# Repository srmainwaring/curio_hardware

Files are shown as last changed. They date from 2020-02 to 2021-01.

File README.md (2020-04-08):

# Curio Hardware

Addition parts for a Sawppy rover.

## Overview

This repository contains [FreeCAD](https://www.freecadweb.org/) and
STL files for additional accessories for
[Roger Chen's Sawppy rover](https://github.com/Roger-random/Sawppy_Rover).

The parts have been printed on a Prusa i3 mk3S printer using PTEG
filament. G-code was generated using PrusaSlicer configured with the
print settings described in the
[Sawppy Rover documentation](https://github.com/Roger-random/Sawppy_Rover/blob/master/docs/Print%20Overview.md).

## Bogie stops

The stops are to prevent the bogie arm attached to the middle wheel
rising from rising above the rear rocker arm and damaging the
servo wires.

***Printing:***

- Approx. 40 mins for a pair

***Assembly:***

Fit the stops with a M3 threaded heat insert and afix to the inside
slot of each front bogie arm with a M3 square nut and M3 x 16mm socket
head screw.

## RPLidar A1 mounting plate and cowling

The mounting plate and cowling are for fixing a Slamtec RPLidar A1
onto a Sawppy rover.

***Printing:***

- Mounting plate: approx. 2h 30min
- Cowling: approx. 5h

The cowling requires support and will need to be cleaned up post-print.
It may help to clean the holes in both the mounting plate and cowling
with a 3mm drill.

***Assembly:***

The mounting plate attaches to the front left corner of the main
body box. You will need to remove the body corner to insert
8 M3 square nuts into the T-slot into which
8 M3 x 16mm socket head screws will be fixed.

Prior to attaching the mounting plate to the rover, fix the
RPLidar A1 USB-to-TTL board to the underside of the
mounting plate. Make sure it is aligned so the ribbon cable comes up
and through the rectangular slot. Attach the ribbon cable to the
laser scan assembly then fix to the top of the plate. You may also
wish to insert the micro-USB cable into the USB-to-TTL board before
attaching as it is awkward (but not impossible)
to attach once assembled.

Place the cowling over the laser scanner and check the motor is clear
and the scan drum can rotate without obstruction. Then fix the
cowling and mounting plate to the rover body box with the
M3 x 16mm screws.

## Battery holder

This is an additional battery holder for securing a 5V 2A power bank
for the Raspberry Pi. It has been dimensioned to hold a
RAVPower RP-PB052 22000mAh power bank, but can be easily modified
for other models.

***Printing:***

- Approx. 4h for a pair of supports.

***Assembly:***

The battery holder comprises a pair of supports and is mounted on the
side rails of the main body box to the rear of the differential brace.
You will need to remove a rear body corner to insert 8 M3 square nuts
into the T-slot into which 8 M3 x 12mm socket head screws will be fixed.
Insert 4 M3 square nuts into the underside slot of the upper rail and
4 M3 square nuts into the topside slot of the lower rail.

The first support can be set up flush against the differential brace.
There should be a gap of approx. 40 mm between the two supports.  

## License

This software is licensed under the BSD-3-Clause license found in
the LICENSE file in the root directory of this source tree.

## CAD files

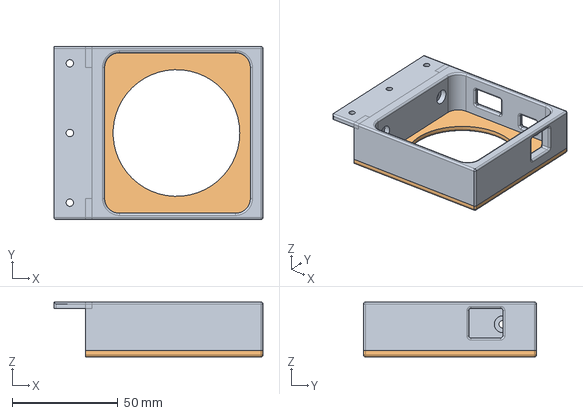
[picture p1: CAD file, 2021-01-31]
freecad/TPLinkAC750_Tray.FCStd
99.0 x 82.0 x 26.0 mm
TPLinkAC750_Tray_Body
TPLinkAC750_TrayBase_Body

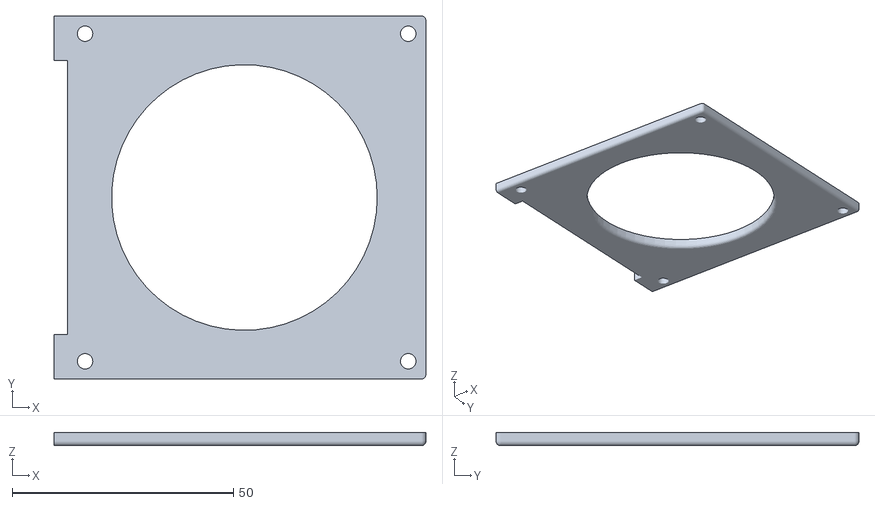
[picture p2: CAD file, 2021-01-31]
stl/TPLinkAC750_Tray_Base.stl
84.0 x 82.0 x 3.00

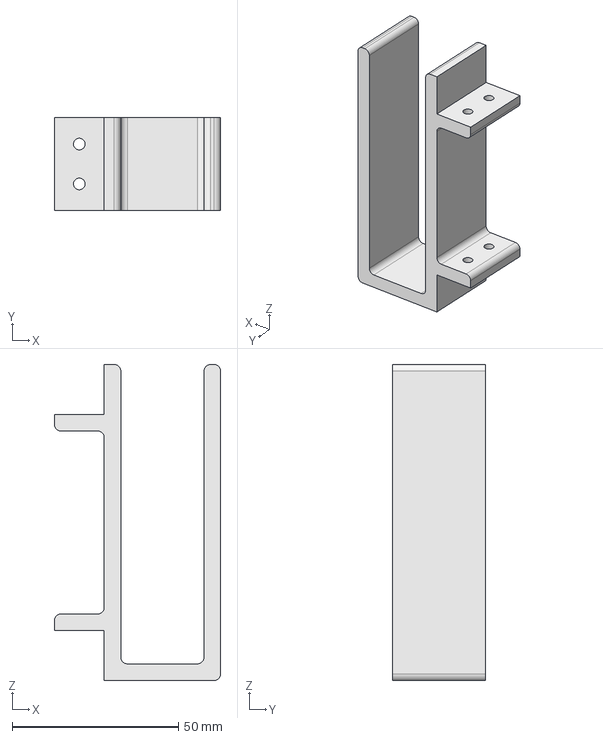
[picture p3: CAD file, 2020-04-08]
freecad/Battery_Holder.FCStd
50.0 x 28.0 x 95.0 mm

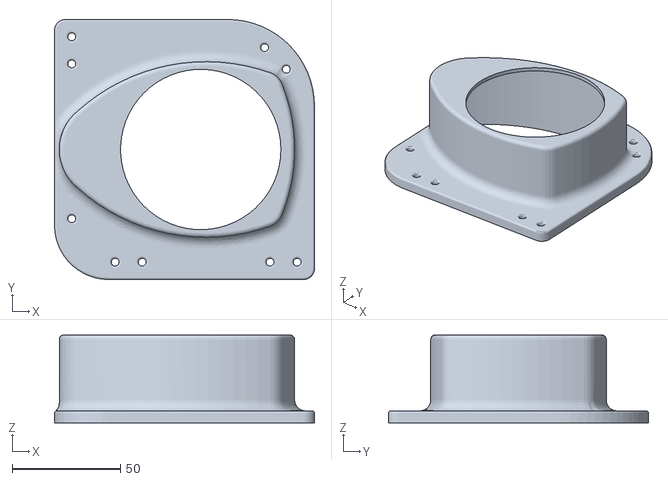
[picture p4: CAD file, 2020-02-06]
stl/RPLidarA1_Cowling.stl
120.0 x 120.0 x 40.6

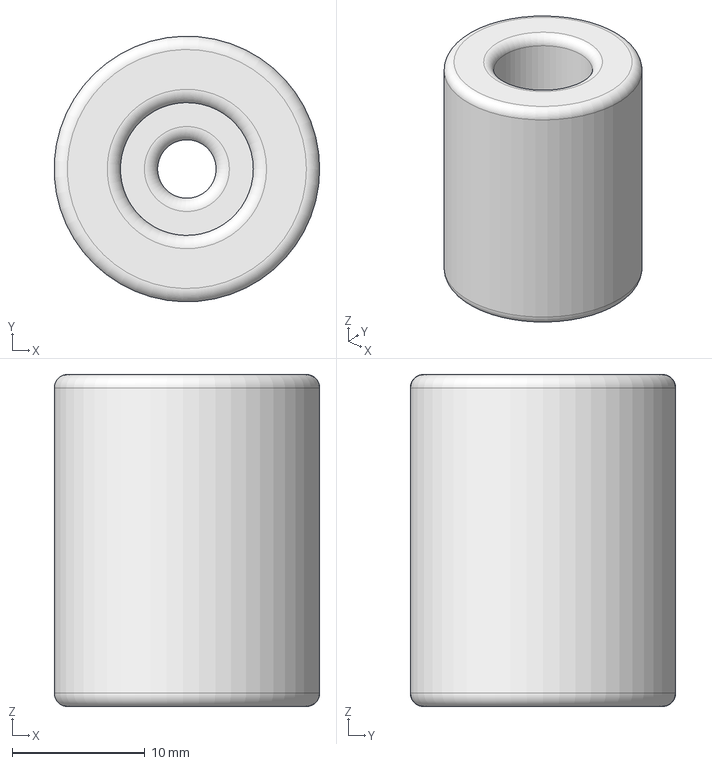
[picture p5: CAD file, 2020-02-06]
freecad/Bogie_Stop.FCStd
20.0 x 20.0 x 25.0 mm

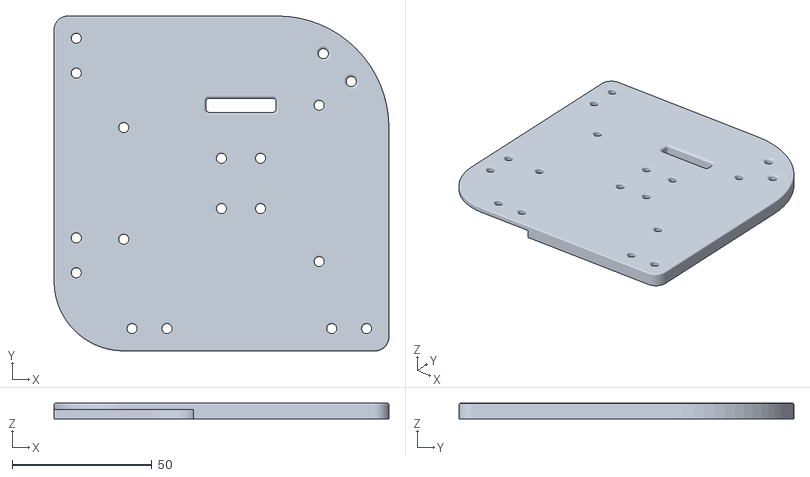
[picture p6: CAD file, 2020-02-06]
stl/RPLidarA1_Mount.stl
120.0 x 120.0 x 5.60

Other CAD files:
stl/Battery_Holder.stl
stl/Bogie_Stop.stl
stl/TPLinkAC750_Tray.stl

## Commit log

2020-02-06 Add documentation and CAD files for additional parts.
    1. Add bogie stop CAD and STL files.
    2. Add RPLidar A1 mounting plate and cowling CAD and STL files.
    [Bogie_Stop.FCStd, Bogie_Stop.stl, RPLidarA1_Cowling.stl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]
2020-04-08 Add FreeCAD and STL files for a power bank holder.
    [Battery_Holder.FCStd, Battery_Holder.stl]
2020-05-02 Add design for a tray to hold a TPLinkAC750 mobile WiFi network box.
    [TPLinkAC750_Tray.FCStd, TPLinkAC750_Tray.stl, TPLinkAC750_Tray_Base.stl]
